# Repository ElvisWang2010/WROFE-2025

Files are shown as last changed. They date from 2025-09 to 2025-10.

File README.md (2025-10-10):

<div align="center">
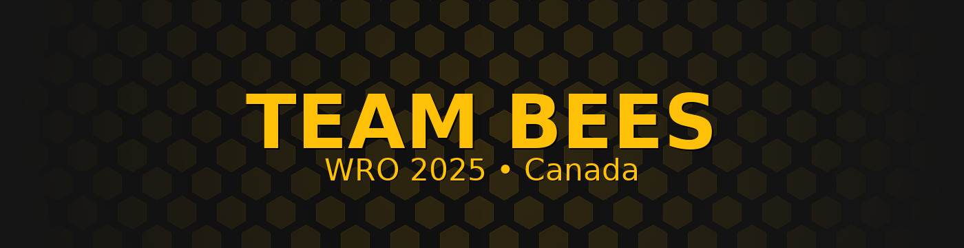
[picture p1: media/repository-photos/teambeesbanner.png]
teambeesbanner

</div>

<p align="center">
  <a href="#"><a>
  <a href="#"><a>
  <a href="#"><a>
  <a href="#"><a>
</p>

teambeesgif

<a href="https://www.youtube.com/@TeamBees2025Panama">

---

# Table of Contents

<details open>
<summary><h3>Team</h3></summary>

- [Team Members](#team-members)  
- [Team Photo](#team-photo)

</details>

---

<details>
<summary><h3>Hardware & Build</h3></summary>

- [Complete Construction Manual](#complete-construction-manual)  
- [Machinery & Components](#machinery)
- [3D Design](#3d-design-and-fabrication)
- [Assembly Gallery](#assembly-gallery)

</details>

---

<details>
<summary><h3>Mobility</h3></summary>

- [Mobility Management](#mobility-management)  
  - [Chassis](#chassis)  
  - [Drive System](#drive-system)  
  - [Motor](#motor)  
  - [Electronic Speed Controller (ESC)](#electronic-speed-controller-esc)  
  - [Steering](#steering)  
  - [Servo Motor](#servo-motor)

</details>

---

<details>
<summary><h3>Power</h3></summary>

- [Power Management](#power-management)  
  - [Battery](#battery)
  - [Power Ratings Table](#power-ratings-table)
  - [Electrical Wiring](#electrical-wiring)  
  
</details>

---

<details>
<summary><h3>Sensors & Perception</h3></summary>

- [Sense Management](#sense-management)
- [Expansion Board](#expansion-board)
- [Raspberry Pi](#raspberry-pi-5)
- [Camera](#camera)    
- [LiDAR](#lidar)

</details>

---

<details>
<summary><h3>Software</h3></summary>

- [Frameworks](#software)  
  - [Python 3.0](#python-30)  
  - [ROS 2 Humble](#ros2-humble)  
- [Libraries](#libraries)  
  - [Picamera2](#picamera2)  
  - [OpenCV](#opencv)  
  - [cv_bridge](#cv_bridge)  
  - [Time](#time)  
  - [Numpy](#numpy)  
  - [ROS Robot Controller SDK](#ros_robot_controller_sdk)

</details>

---

<details>
<summary><h3>WRO Challenges</h3></summary>

- [Open Challenge](#open-challenge)  
- [Obstacle Challenge](#obstacle-challenge)

</details>

---
</br>

## Experience

Throughout our preparation for the WRO Future Engineers competition, each of us gained new skills and experiences that went far beyond what we expected.

Months before the competition, Elvis was learning how to 3D model and 3D print custom parts for our robot. He also explored electronics in depth, learning how to wire, solder, and integrate components safely and effectively.

Harry focused on the software side, diving into ROS 2 to learn how to create nodes, build packages, and structure entire workspaces for complex multi-node communication.

Ryan improved his programming skills during the project. He learned how to properly use and navigate GitHub. He also expanded into 3D modeling.

</br>

## Our Coach
<table>
<tr>
  <td align="center" width="40%">
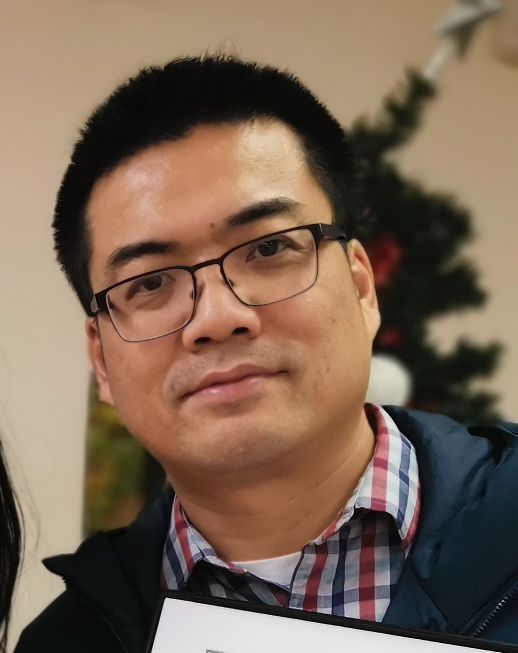
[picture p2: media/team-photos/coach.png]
    <br>
    <em>Our Coach — Mentor and Guide</em>
  </td>

  <td valign="top" width="60%">

  ### Information
  - Head coach of Robotics Competitions, including FLL (First LEGO League),  WRO (World Robotics Olympiad) Robo Sports, Future Engineers, and Robo Mission. Led teams in winning multiple national, international robotics, and programming awards.
  - Over 20 years of IT industry experience as a software engineer working internationally.
  - MSc in Electrical & Computer Engineering from the University of Alberta.
  - BSc in Mathematics from Peking University.
  - Founder of Explorer Robotics, a local robotics club in Ajax and Whitby, teaching coding, AI, robotics, etc.
  </td>
</tr>
</table>



A special thanks goes out to our amazing coach, who has been the foundation of our journey. He not only introduced us to ROS2, but was also the first person to open our eyes to the WRO Future Engineers competition and the broader world of robotics. 

## Team Members

<table width="100%" style="border:2px solid #FFC107; border-radius:12px; margin:12px 0;">
  <tr>
    <td width="28%" align="center" style="padding:12px; border-right:6px solid #111;">
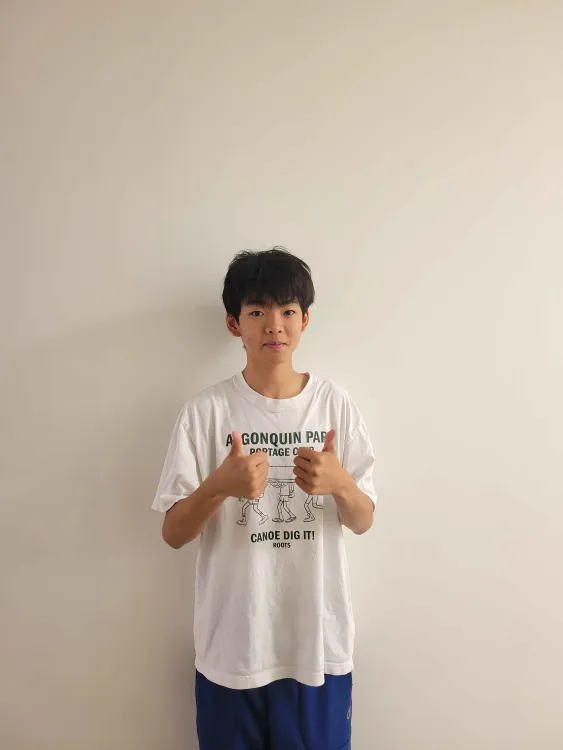
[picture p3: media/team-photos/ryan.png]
Ryan
      
    </td>
    <td width="72%" style="padding:12px 16px;">
      <h3 style="margin:0 0 6px 0;">Ryan</h3>
      <div><b>Role:</b> Documenter/Programmer</div>
      <div><b>Strengths:</b> Writing, Hardworker.</div>
      <p style="margin-top:8px;">
        <b>About Me:</b> Hi! I'm Ryan. I'm 14, love to write, play badminton, listen to music, and travel. I've been involved in robotics for nearly a decade and participated in both FLL and WRO Robo Mission. I also have a 4-year-old golden retriever 😊.
      </p>
    </td>
  </tr>
</table>

<table width="100%" style="border:2px solid #FFC107; border-radius:12px; margin:12px 0;">
  <tr>
    <td width="28%" align="center" style="padding:12px; border-right:6px solid #111;">
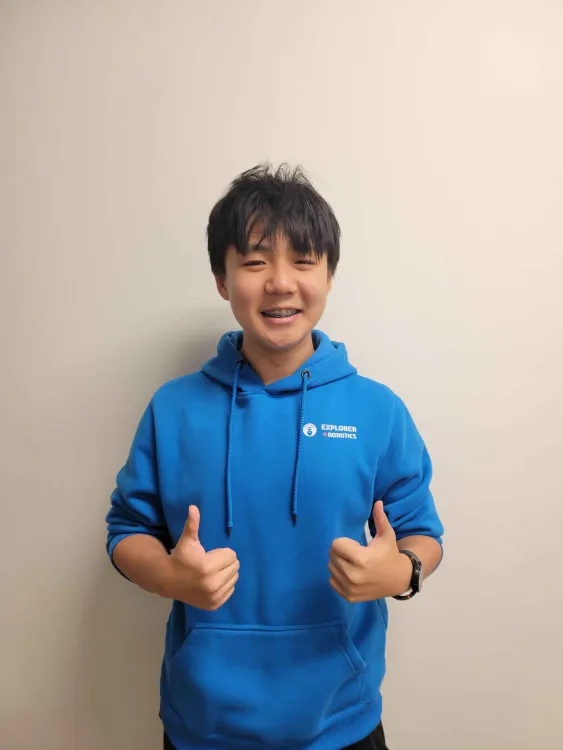
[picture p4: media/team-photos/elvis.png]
Elvis
      
    </td>
    <td width="72%" style="padding:12px 16px;">
      <h3 style="margin:0 0 6px 0;">Elvis</h3>
      <div><b>Role:</b> Builder/Programmer</div>
      <div><b>Strengths:</b> CAD, Fabrication, Team Player, Hardworker.</div>
      <p style="margin-top:8px;">
        <b>About Me:</b> Hi, my name is Elvis. I'm 14. I enjoy building and 3D modeling various objects with Fusion 360. I've been with Explorer Robotics ever since I was 8 years old, and I love to work and play Clash Royale.
      </p>
    </td>
  </tr>
</table>

<table width="100%" style="border:2px solid #FFC107; border-radius:12px; margin:12px 0;">
  <tr>
    <td width="28%" align="center" style="padding:12px; border-right:6px solid #111;">
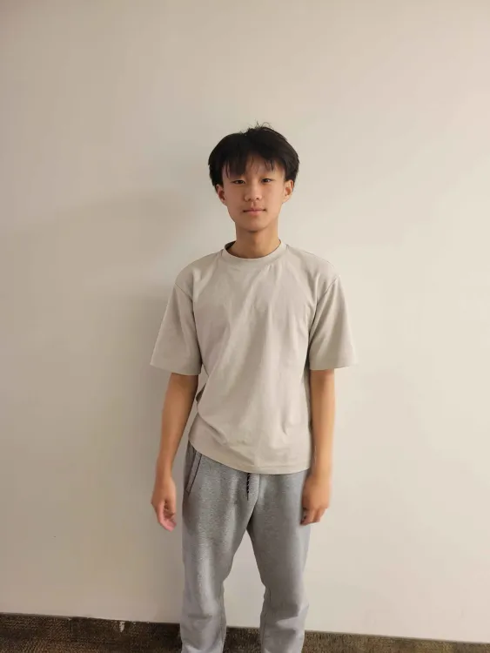
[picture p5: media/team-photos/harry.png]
Harry
      
    </td>
    <td width="72%" style="padding:12px 16px;">
      <h3 style="margin:0 0 6px 0;">Harry</h3>
      <div><b>Role:</b> Programmer/Documenter</div>
      <div><b>Strengths:</b> Python, Problem Solver, Patience, Hardworker.</div>
      <p style="margin-top:8px;">
        <b>About Me:</b> Hey! I'm Harry. I've been coding for over half a decade and enjoy swimming, having competed in various swimming competitions. I also like to play badminton.
      </p>
    </td>
  </tr>
</table>

</br>

## Introduction
Team Bees is a 1st year group of high-school students from Ontario, Canada, passionate about robotics and self-driving technologies. Our car was designed and programmed to complete both the Open and Obstacle Challenges of WRO 2025 Future Engineers. After only placing 5th in Ottawa Nationals, we advanced to Panama Internationals, representing our country.

Our objective is to design a low-cost, fully autonomous miniature car using accessible components and open-source software, integrating vision, IMU, and LiDAR for perception and ROS 2 Humble for system control.

# Team Photo

<table width="100%" style="border:2px solid #FFC107; border-radius:12px; margin:8px 0;">
  <tr>
    <td align="center" style="padding:14px;">
      <div style="border:2px dashed #FFC107; border-radius:10px; padding:24px; height:320px; display:flex; align-items:center; justify-content:center;">
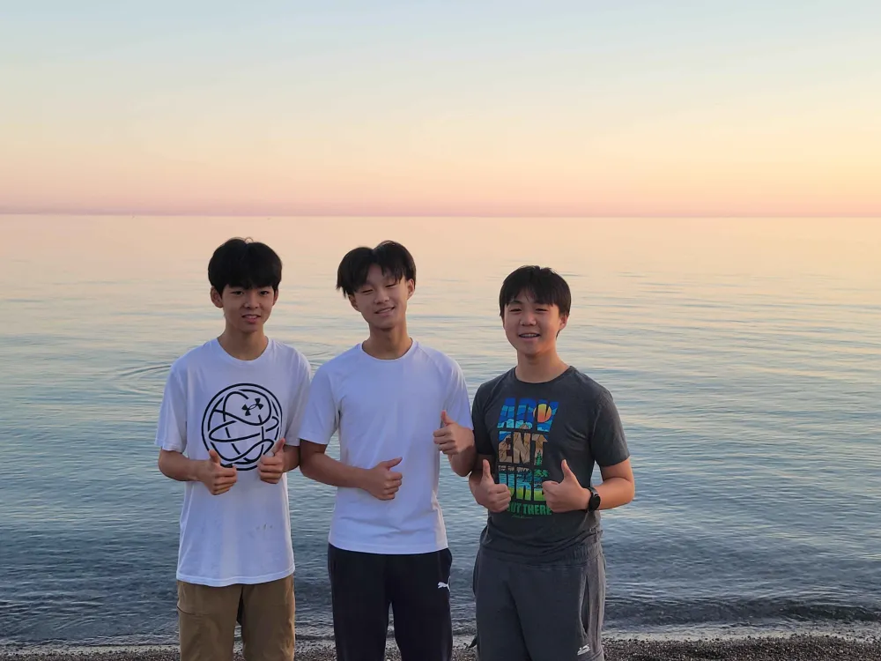
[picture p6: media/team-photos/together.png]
        <b></b>
      </div>
      <div style="margin-top:8px; color:#444;"><em>Team Bees — WRO 2025 Future Engineers (Nationals → Panama)</em></div>
    </td>
  </tr>
</table>

</div>

</br>

---

</br>

## Complete Construction Manual

The WRO Future Engineers is a competition for self-driven vehicles. Students in the 15- to 19-year-old age group need to design a model of a car, equip it with electromechanical components, and program it so that it can drive autonomously on the track, avoiding obstacles.

More details about the competition can be found on [the official site of WRO Association](https://wro-association.org/competition/2025-season/#rules).

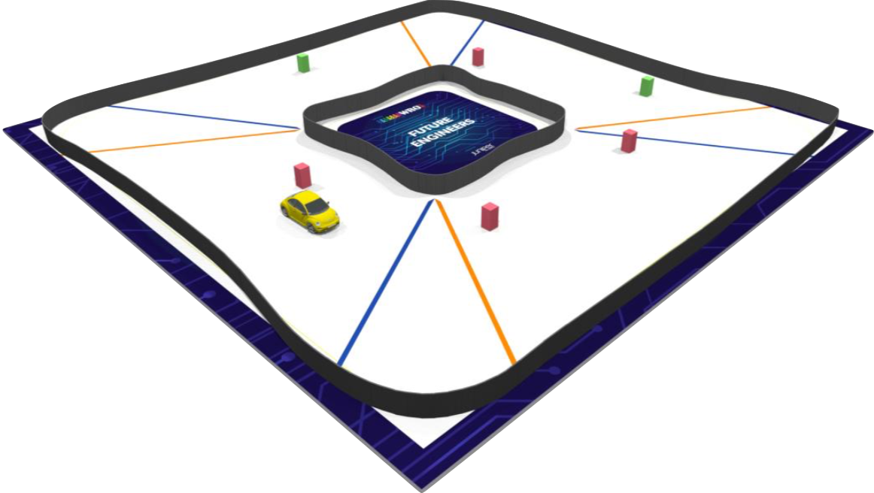
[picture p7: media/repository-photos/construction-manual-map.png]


The materials are intended to be built with the [Mkdocs](https://www.mkdocs.org/) site generator.

The example of the site is accessible at https://world-robot-olympiad-association.github.io/future-engineers-gs/.

</br>

---

</br>

## Machinery 
### Components
| Name | Product | Price (CAD)|
| --- | --- | --- |
| RC Car Battery | [`Gens Ace 1300mAh Battery`](https://genstattu.com/gens-ace-1300mah-2s-7-4v-45c-g-tech-lipo-battery-pack-with-deans-plug/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) | $20.6 | 
| Drive Motor | [`Furitek Micro Komodo 1212 3450KV Brushless Motor`](https://furitek.com/products/furitek-micro-komodo-1212-3456kv-brushless-motor-with-15t-steel-pinion-for-fury-wagon-fx118) | $35 |
| Servo Motor | [`HS-5055MG 11.9g Metal Gear Digital Micro Servo`](https://hitecrcd.com/hs-5055mg-economy-metal-gear-feather-servo/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) | $25 |
| ESC | [`Furitek Lizard Pro 30A/50A ESC`](https://furitek.com/products/combo-of-furitek-lizard-pro-30a-50a-brushed-brushless-esc-for-axial-scx24-with-bluetooth) | $80 |
| Camera | [`5MP 1080P HD Camera with OV5647 Sensor`](https://www.amazon.ca/dp/B0D324RKRZ?ref=ppx_yo2ov_dt_b_fed_asin_title) | $35 |
| Raspberry Pi 5 8GB | [`Raspberry Pi 5`](https://www.amazon.ca/RasTech-Raspberry-Pi-refroidisseur-inclus/dp/B0DQX6JPVM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) | $170 |
| Expansion Board | [`RRC Lite Controller`](https://www.hiwonder.com/products/rrc-lite?srsltid=AfmBOoqZuQkdiCruulYju-KXoSowMik5Ov_Vs3-_8TA4Bm_luvoK6Oxn) | $40 |
| Switch | [`DaierTek ON Off Round Rocker Switches`](https://www.amazon.ca/DaierTek-Listed-Switches-Automotive-KCD1-5Pack/dp/B07S1MV462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) | $2.6 |
| Wheels | [`Abendor 6 Spoke Wheel Rims`](https://www.amazon.ca/Abendor-Spoke-Narrow-Aluminum-Wltoys/dp/B09ZYVGYB4?th=1) | $31.6 |

*Note: The switch is $13 for 5. 13/5 = 2.6.*

**Total:** $439.8 *No Tax*

**With Tax:** $496.97

---

### Tools and Equipment
| Name | Product | Price (CAD)|
| --- | --- | --- |
| 3D Printer | [`Bambu Lab X1 Carbon 3D Printer`](https://genstattu.com/gens-ace-1300mah-2s-7-4v-45c-g-tech-lipo-battery-pack-with-deans-plug/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) | $1289 | 
| Soldering Kit| [`TOAUTO DS90 Soldering Station`](https://www.amazon.ca/FASTTOBUY-Soldering-Station-194%C2%B0F-896%C2%B0F-Temperature/dp/B082HP4513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) | $90 |
| Screws, Screwdriver, Pliers, etc. | n/a | $~35 |  
| Fillament 1kg | [`EconoFil™ Standard PLA Filament`](https://www.inksmith.ca/collections/filament/products/econofil-standard-pla-filament-black-1-75mm-1-kg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) | $26 |  

**Total:** $~1440 *No Tax*

**With Tax:** $~1627.2

---

### Summary of Cost
| Category | Price (CAD) No Tax| Price (CAD) Tax Included|
| --- | --- |----|
| Components | $439.8| $496.97 |
| Tools and Equipment | $1440| $1627.2 |
| Shipping | $~100 (*not taxed*)| $~100 (*not taxed*) |

**Grand Total** : $1979.8 CAD *No Tax* 

**With Tax** : $2224.17 CAD

</br>

---

## 3D Design and Fabrication

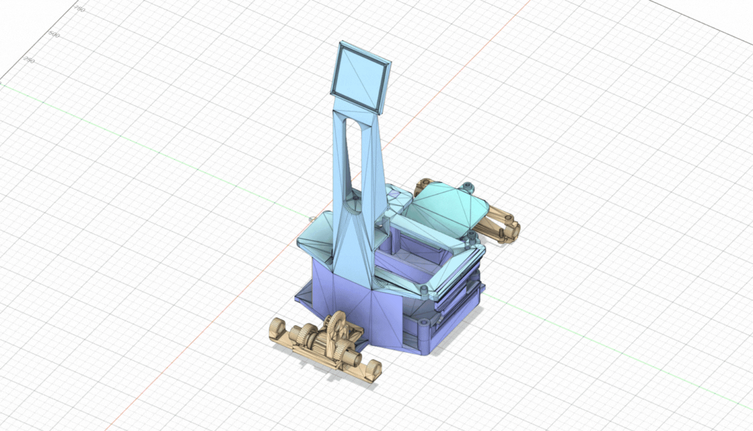
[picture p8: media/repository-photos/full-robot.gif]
|  |
|:--:|
| *Fully 3D printed design, every component custom designed* |

### Overview  
- 3D printing played a key role in our project, allowing us to design, prototype, and refine custom mechanical parts with precision and speed.  
- All major structural components, including the LiDAR mount, steering system, and motor mechanism, were modeled in Fusion and fabricated using a PS1 Bambu Lab printer with PLA filament.  
- The ability to produce rapid design iterations helped us fine-tune geometry, fit, and strength throughout testing.

---

### Printing Parameters  

| Setting | Value |
|---|---|
| Printer | [`Bambu Lab X1 Carbon`](https://ca.store.bambulab.com/products/x1-carbon?id=546459056505716744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) |
| Material | PLA (Bambu Lab Basic) |
| Nozzle Temperature | 230 °C |
| Bed Temperature | 65 °C (Textured PEI Plate) |
| Filament Diameter | 1.75 mm |
| Flow Ratio | 0.96 |
| Max Volumetric Speed | 12 mm³/s |
| Layer Height | 0.2 mm |
| Nozzle Diameter | 0.4 mm |
| Infill Density | 15 % |

---

### Why PLA?  

| Material | Strength | Heat Resistance | Printability | Availability | Notes |
|:--:|:--:|:--:|:--:|:--:|:--|
| PLA | Medium | Low | Very Easy | Widely Available | Ideal for prototypes and low-stress components. Excellent surface finish and easy to reprint. |
| PETG | High | Medium | Moderate | Common | Stronger and more flexible, but harder to print cleanly. Useful for parts under stress. |
| ABS | High | High | Difficult | Common | Better heat resistance, but warps easily and requires a heated enclosure. |
| Nylon / CF-Nylon | Very High | High | Difficult | Limited | Excellent strength and flexibility, but expensive and requires high-end printers. |

</br>

PLA was chosen for its ease of use, low cost, and availability, allowing quick iteration without sacrificing accuracy.  
It provided reliable performance for our robot, where temperature resistance and high flexibility were not critical factors.  

---

</br>

## Assembly Gallery

<table>
  <tr>
    <td align="center" style="border:1px solid #ddd; padding:15px;">
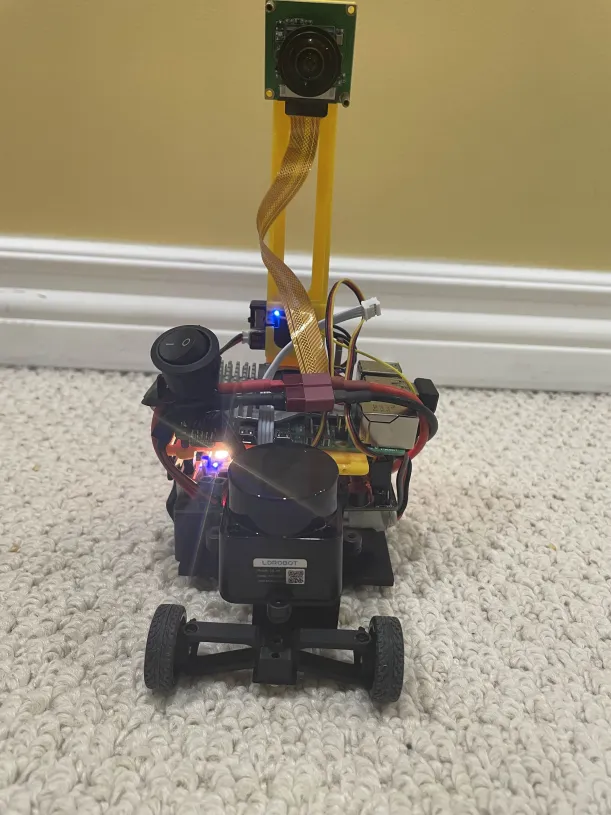
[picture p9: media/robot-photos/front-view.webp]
    <br/>
      <em><strong>Front View</strong><br>Shows the overall profile and front-facing components.</em>
    </td>
    <td align="center" style="border:1px solid #ddd; padding:15px;">
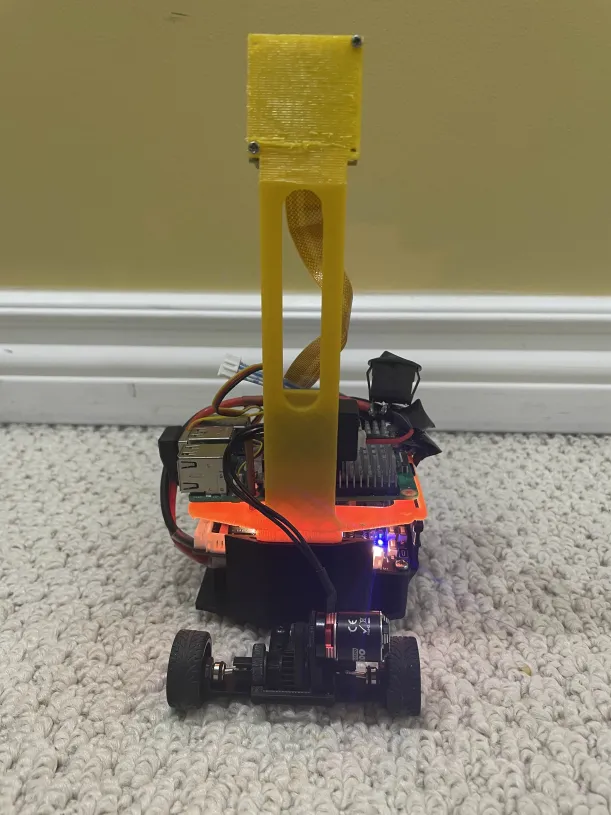
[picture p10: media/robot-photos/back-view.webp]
      <br/>
      <em><strong>Rear View</strong><br>Shows the drive wheels and rear motor assembly.</em>
    </td>
    <td align="center" style="border:1px solid #ddd; padding:15px;">
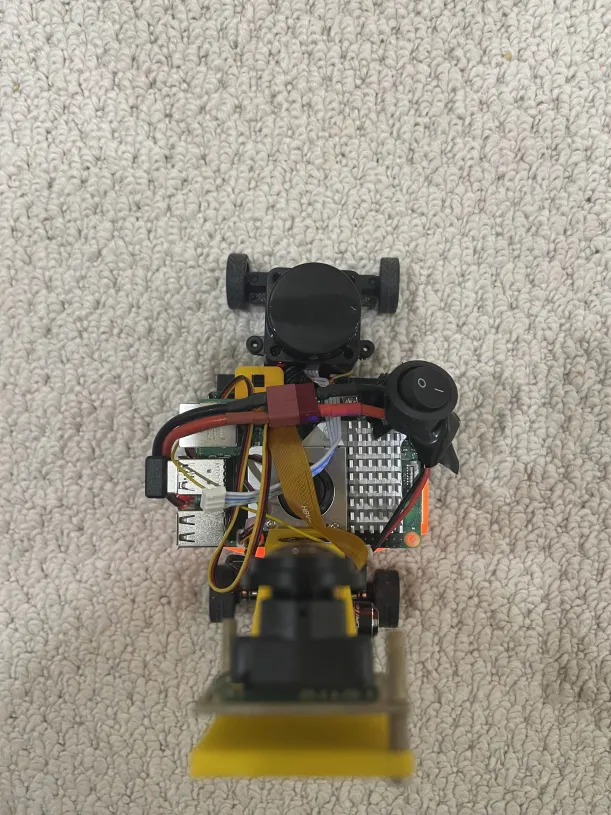
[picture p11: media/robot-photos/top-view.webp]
     <br/>
      <em><strong>Top View</strong><br>Shows the layout of all major components on the upper chassis.</em>
    </td>
  </tr>
  <tr>
    <td align="center" style="border:1px solid #ddd; padding:15px;">
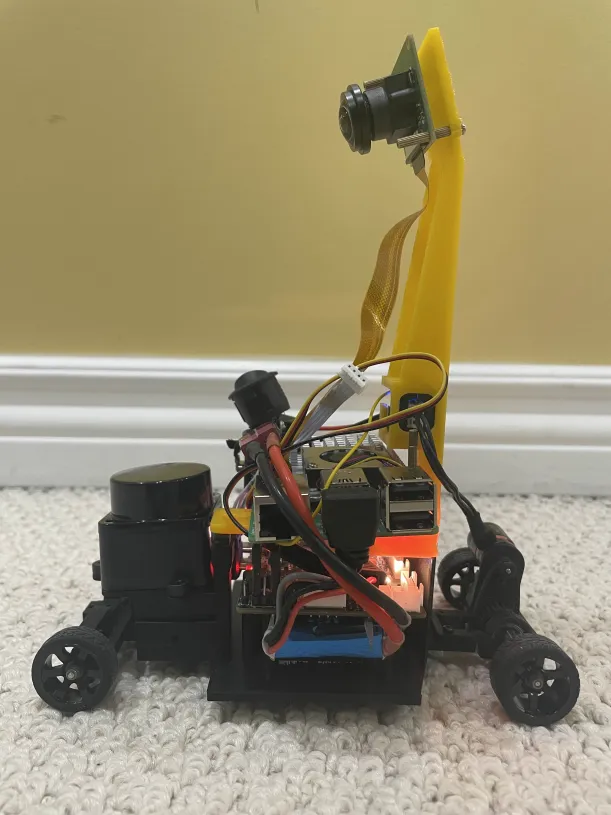
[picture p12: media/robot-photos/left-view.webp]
     <br/>
      <em><strong>Left Side View</strong><br>Shows the side profile and left-side components.</em>
    </td>
    <td align="center" style="border:1px solid #ddd; padding:15px;">
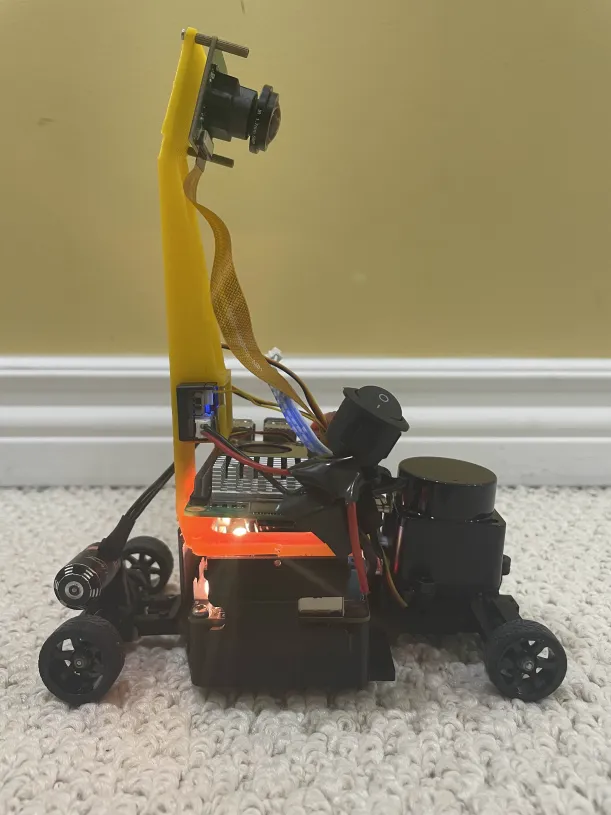
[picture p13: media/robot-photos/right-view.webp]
      <br/>
      <em><strong>Right Side View</strong><br>Shows the side profile and right-side components.</em>
    </td>
    <td align="center" style="border:1px solid #ddd; padding:15px;">
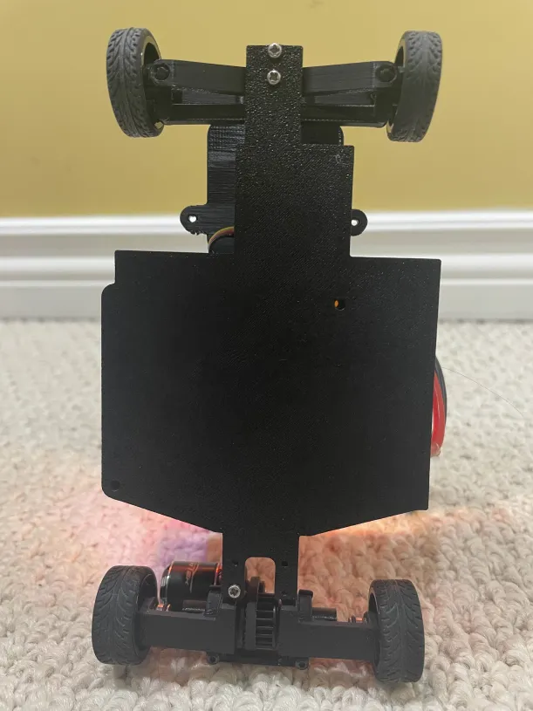
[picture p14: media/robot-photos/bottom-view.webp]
      <br/>
      <em><strong>Bottom View</strong><br>Shows the underside, wheel mounting, and lower chassis.</em>
    </td>
  </tr>
</table>

</br>

---
</br>

# Mobility Management
This section covers and houses all components that help or allow our robot to move and steer. It includes the steering system for directional control, the electronic speed controller (ESC) to manage motor power, the main motor for movement, a servo motor for precise adjustments like steering, and the chassis, which is the base to hold and support all these parts securely.

</br>

## Chassis 

We have had many chassis prototypes. For our first build, we selected the **ACXWA CD chassis**, a non-prebuilt frame originally crafted with a modular design to provide adjustable lengths between 1/28 and 1/24 scale. 
However, later on, we opted to redesign the entire chassis, 3D printing and customizing our entire robot in the process, excluding a few minor metal modules (pins, screws, etc.).

</br>

<table>
  <tr>
    <td width="48%" valign="top">
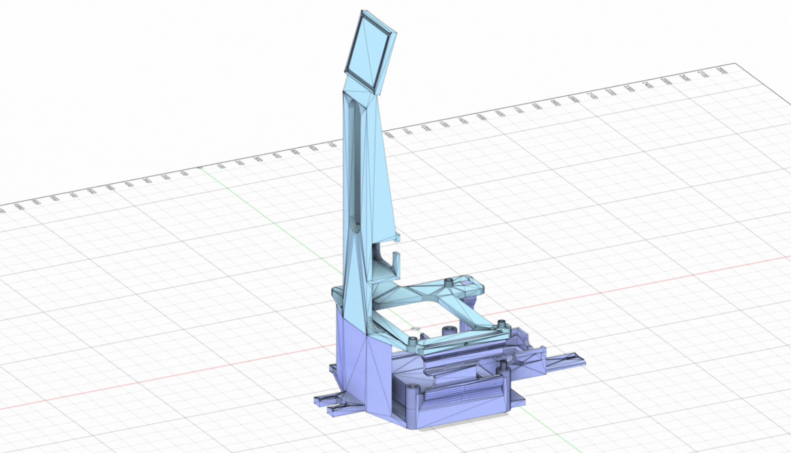
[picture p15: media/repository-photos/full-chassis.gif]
Chassis
      
      <p align="center"><em>Redesigned structural chassis assembly</em></p>
    </td>
    <td width="52%" valign="top">

### Notable Features 

- Modular design allows quick attachment of sensors, electronics, and mounts.  
- Integrated mounting rails support camera and LiDAR at optimized heights for field visibility.    
- Designed to keep the center of gravity low, improving balance and traction during movement.  

    </td>
  </tr>
</table>

---

### Chassis Limitations

Although the redesigned chassis offers significant improvements in modularity and sensor integration, it is not without challenges. The tall vertical structure increases air drag and introduces slight flex during high-speed operation, particularly when carrying additional sensors at the top. The frame’s precision mounting points demand tight tolerances, making small print variations more noticeable during assembly. Cable management also becomes more complex due to limited internal routing space, requiring external clips or channels to maintain a clean layout. 

---
### Utilization
Our custom 3D-printed chassis was carefully designed to house all the key electronic components required for our autonomous car. The lower compartment securely holds the battery and a part of the servo motor, ensuring a low center of gravity for better stability and weight distribution. Just above that, a dedicated mounting section was created for the RRC (ROS Robot Controller) expansion board. On the upper frame, we integrated a platform for the Raspberry Pi 5, which serves as the main processing unit for camera and sensor data. The long arm at the vertex of the chassis secures our camera. Right beneath it, there is a custom slot specifically designed to secure our ESC.

</br>

---

</br>

### Wheels
<div align="center">

<table>
  <tr>
    <td style="border: 200px solid black; padding: 5px;">
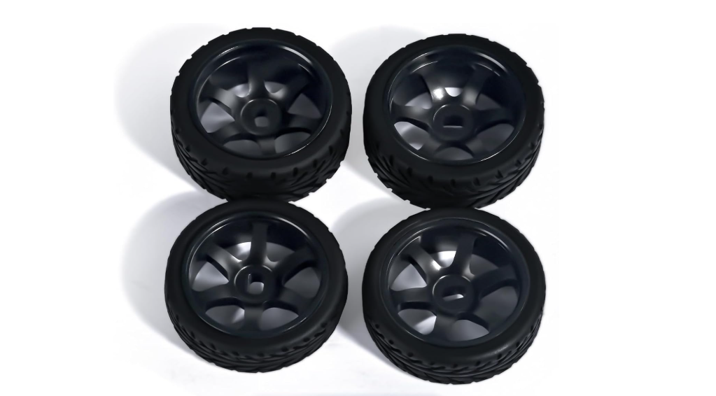
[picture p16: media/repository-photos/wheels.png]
      
    </td>
  </tr>
</table>

</div>

<p><strong>Where to Buy:</strong> <a href="https://www.amazon.ca/Abendor-Spoke-Narrow-Aluminum-Wltoys/dp/B09ZYVGYB4?th=1" target="_blank">Click Here</a></p>

</br>

Our previous wheels came with the ACXWA chassis; however, the wheels were designed to drift, and we needed to switch them out for grippier wheels. This switch had an immediate effect on the car's performance. With better traction, the vehicle could accelerate harder without losing control. It could also maintain a steady speed through turns. This made handling more predictable, which was especially important for precise tasks like navigating pillars and parking.

The new wheels also improved efficiency. With less energy wasted on wheel slip, the motor’s output went more directly into forward motion. This not only made the car feel faster but also reduced strain on the drivetrain during long runs. As a result, we had a setup that was both quicker and more reliable in competition.

</br>

## Drive System

Our car uses a rear wheel drive (RWD), meaning that the motor's power is transmitted to the back wheels rather than the front. This configuration provides many benefits to the car.

</br>

### Benefits
- Better weight distribution. This is because the front wheels handle steering, and the rear wheels help with propulsion, which helps the car remain more balanced during acceleration and turning.
- RWD also provides a stronger grip on surfaces. Since the rear of the robot is heavier, the back wheels get pressed into the ground, providing for more traction and therefore enhancing the grip.
- Since the front wheels are only used for steering, the car can turn more precisely, as there is no motor interference.

</br>

## Motor

---

<table>
<tr>
  <td width="35%" valign="top">

  ### Physical Qualities
  | Field          | Value                              |
  |----------------|------------------------------------|
  | **Product Title** | Furitek Micro Komodo 1212 3450KV |
  | **Size**          | 15.5 × 20.6 mm                   |
  | **Weight**        | 17.5 g                           |
  | **Physical State**| Brushless Outrunner (12-slot)    |

  </td>

  <td width="65%" align="center">
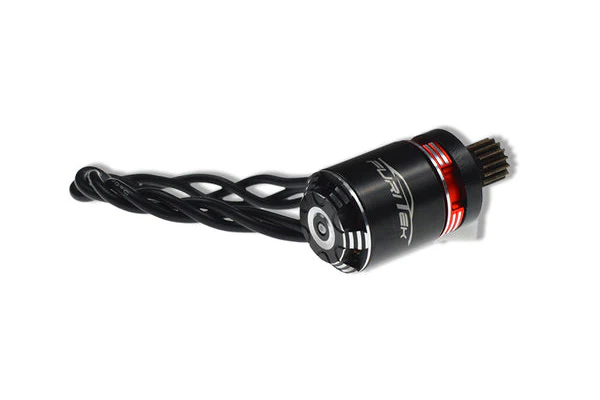
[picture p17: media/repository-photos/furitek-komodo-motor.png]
    <br>
    <em>Furitek Komodo 1212 motor</em>
  </td>
</tr>
</table>

---

<table>
<tr>
<td width="65%" valign="top">

### Reasoning of Purchase
Following a review of suitable brushless options, we selected the Furitek Micro Komodo 1212 3450 KV brushless motor. This motor is compact and lightweight, making it perfect for a small self-driving platform where space and weight impact agility and energy use. Its 12-slot, multipole design distributes torque more evenly during rotation. This results in less cogging, smoother throttle response, and better control at low speeds.

---

### Potential Improvements
- Replace plastic gears with metal gears to withstand sustained, high-speed usage.
- Experiment with 10 : 58 – 14 : 58 combinations to tune the balance between torque and top speed.
- Upgrade or lubricate bearings to reduce friction and improve consistency over multiple heats.
  
</br>

</td>

<td width="35%" valign="top">

### Performance Specifications
- KV: **3450 rpm/V**  
- No-load @10V: **0.7 A**  
- Power: **120 W**  
- Battery: **2–3S LiPo**  
- Resistance: **0.16 Ω**  
- Max Current: **10 A**  
- Slot/Pole: **12**  
- Shaft: **1.5 × 6 mm**  

</td>
</tr>
</table>

---

<p><strong>Where to Buy:</strong> <a href="https://furitek.com/products/furitek-micro-komodo-1212-3456kv-brushless-motor-with-15t-steel-pinion-for-fury-wagon-fx118" target="_blank">Click Here</a></p>

</br>

To secure the motor to the chassis, we 3D printed a motor mechanism with a slot designed to fit the motor's axle.

</br>

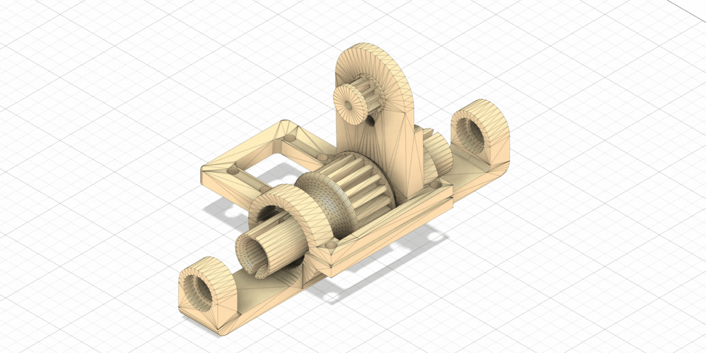
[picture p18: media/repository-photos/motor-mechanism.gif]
|  |
|:--:|
| **Motor Mechanism** |

</br>

This 3D-printed motor gear mount assembly connects the brushless motor to the drivetrain using a fixed spur gear reduction system. The motor’s pinion drives a larger spur gear on the output shaft, which reduces speed and increases torque. The mount has a sturdy motor plate, gear supports that fit bearings, and a reinforced base that keeps both shafts aligned. This setup ensures smooth power transfer and consistent gear meshing. The design reduces energy loss and mechanical vibration from misalignment while remaining lightweight and compact. 

### Potential Improvements
- Implement a stronger motor holder to cut down on vibration and improve stability when it's under load.
- Explore different motor designs to improve performance and reduce weight.

## Electronic Speed Controller (ESC)  
The ESC is a key component that regulates how the motor receives power. It:  
- Controls the motor's speed  
- Manages direction  
- Ensures safe delivery of voltage and current to the motor

This ESC was chosen for its high current capacity, lightweight design, and reliable built-in BEC, making it well-suited for our motor and servo needs.

</br>

<table border="1" width="100%" style="font-size:20px; text-align:left;">
  <tr> 
    <td width="50%" align="center" style="vertical-align:top;"> 
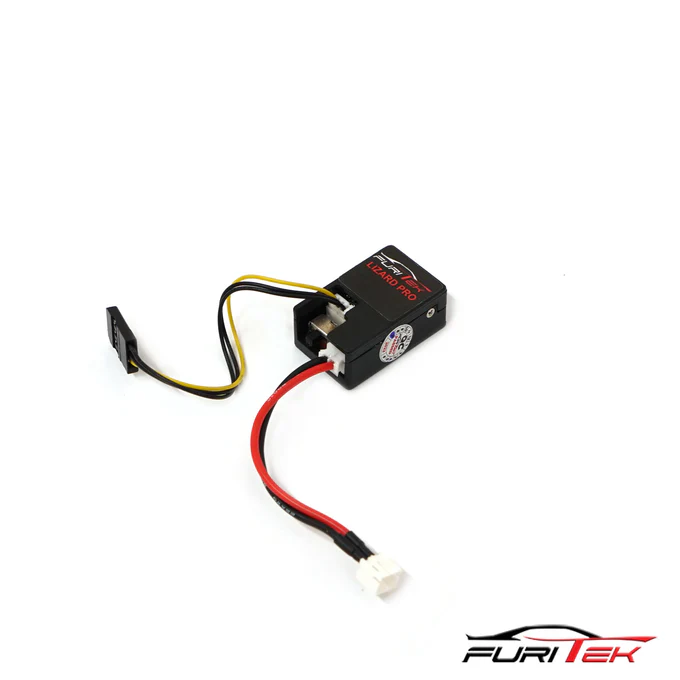
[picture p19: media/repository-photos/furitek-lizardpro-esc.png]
       
    </td> 
    <td width="50%" valign="top" style="vertical-align:top; font-size:20px;"> 
         <h2 style="font-size:28px;">Furitek Lizard Pro 30A/50A ESC</h2> 
      <ul>
        <li><strong>Battery Support:</strong> 2S–3S LiPo</li> 
        <li><strong>BEC:</strong> 5V or 6.5V, 2.5A</li> 
        <li><strong>Constant Current:</strong> 30A</li> 
        <li><strong>Burst Current:</strong> 50A</li> 
        <li><strong>Built-in Power Switch</strong></li> 
        <li><strong>Dimensions:</strong> 28 × 15.5 mm</li> 
        <li><strong>Weight:</strong> 3.7 g</li> 
      </ul> 
    </td> 
  </tr> 
</table>

<p><strong>Where to Buy:</strong> <a href="https://furitek.com/products/combo-of-furitek-lizard-pro-30a-50a-brushed-brushless-esc-for-axial-scx24-with-bluetooth" target="_blank">Click Here</a></p>

</br>

---

## Servo Motor

This servo motor was chosen for its compact size, strong torque, and durable metal gears, making it great for precise steering control.

</br>

<table border="1" width="100%" style="font-size:20px;">
  <tr>
    <td width="50%" align="center" style="vertical-align:top;">
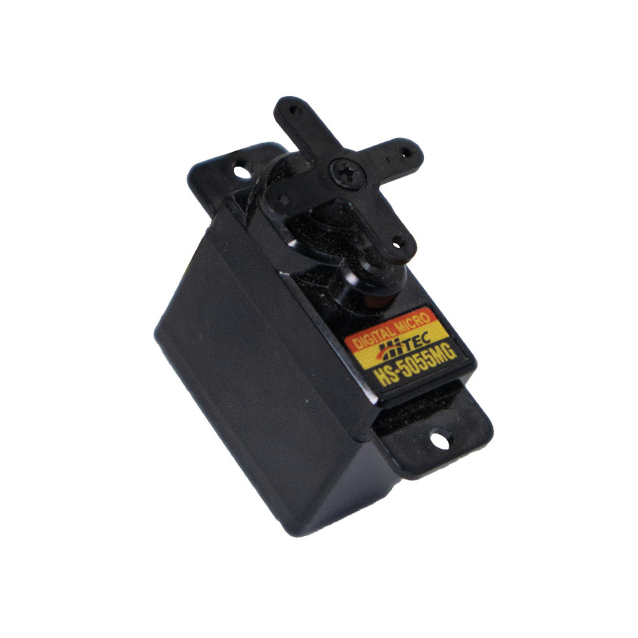
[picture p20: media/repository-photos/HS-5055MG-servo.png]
      
    </td>
    <td width="50%" valign="top" style="vertical-align:top; font-size:20px;">
      <h2 style="font-size:26px;">HS-5055MG 11.9g Metal Gear Digital Micro Servo</h2>
      <ul>
        <li><strong>Operating Voltage:</strong> 4.8V – 6.0V DC</li>
        <li><strong>Max Torque:</strong> 22 oz/in (1.6 kg/cm)</li>
        <li><strong>Speed:</strong> 0.17s/60° @ 6.0V</li>
        <li><strong>Stall Current:</strong> 700 mA</li>
        <li><strong>Gear Material:</strong> Metal</li>
        <li><strong>Weight:</strong> 9.5 g</li>
        <li><strong>Circuit Type:</strong> G1 Programmable Digital</li>
      </ul>
    </td>
  </tr>
</table>

<p><strong>Where to Buy:</strong> <a href="https://hitecrcd.com/hs-5055mg-economy-metal-gear-feather-servo/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" target="_blank">Click Here</a></p>

</br>

### Potential Improvements
- Improve response time. This servo motor is not as quick as higher-end micro servos, which reduces steering precision during sharp turns.
- Upgrade to a higher-torque digital micro servo for more reliable steering.

</br>

## Steering
Our prototype used a commercial chassis. We quickly found that the steering system was inefficient and turned unevenly. To fix this, we built a completely new steering system from scratch, 3D-printing all the components for the precise and balanced control we needed. We developed two different steering designs. The first design includes a mounting frame that attaches the system to the chassis, a servo linkage arm that connects directly to the servo motor, and steering knuckles. However, the second design showed more potential. After testing, it performed better than the first design. This design features an antisway arm, steering knuckles, and a control arm, offering a more consistent turn, easier assembly, and greater durability.

</br>

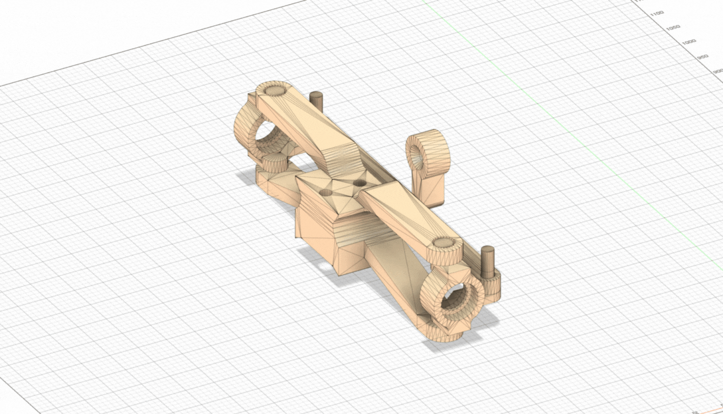
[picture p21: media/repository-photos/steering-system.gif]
|  |
|:--:|
| **Steering System** |

</br>

### Key Improvements Over Stock Design
1. **Symmetry in Motion** – Both left and right wheels now turn at equal angles, reducing understeer/oversteer imbalance.  
2. **Reduced Backlash** – By using strong linkages and tightly toleranced 3D-printed parts, uncontrolled movement is minimized.  
3. **Strength & Durability** – The mounting frame distributes servo torque evenly, reducing wear and preventing chassis flex.  
4. **Precision Control** – The redesigned geometry allows finer servo adjustments to translate directly into steering corrections.
   
</br>

- Add more fillets on corners, reducing stress concentration and preventing cracks.
- Implement brass threaded inserts for screw holes rather than relying on bare plastic.

</br>

### How the Car Moves
When the battery provides power, the ESC manages the electricity sent to the motor. The motor turns this controlled flow of electricity into rotational motion, which makes the car's wheels spin. By changing the voltage and current through the ESC, we can control the car's speed and direction, enabling it to move forward, backward, accelerate, slow down, or reverse.

At the same time, the servo motor handles steering. It changes the angle of the front wheels through the steering system, allowing the car to turn left or right accurately.

---

</br>

# Power Management

The robot’s power system is carefully designed to balance performance and efficiency, ensuring stable operation throughout the challenge.

</br>

## Battery

---

<table>
<tr>
  <td valign="top" width="35%">

  ### Physical Qualities
  | Field | Value |
  |--------|--------|
  | Product Title | Gens Ace 1300mAh 2S 7.4V 25C LiPo |
  | Size | 70.9 × 35.2 × 14.5 mm |
  | Weight | 90 g |
  | Type | 2S1P LiPo Battery |
  | Connector | T-Style (Battery), G-Tech Smart (Balance) |

  </td>

  <td align="center" width="65%">
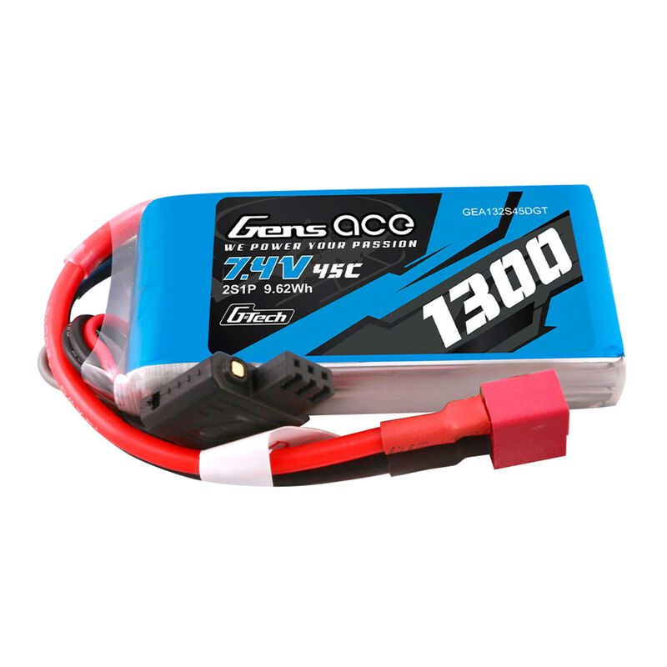
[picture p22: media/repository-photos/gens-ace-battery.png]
    <br>
    <em>Gens Ace 1300mAh 2S LiPo Battery</em>
  </td>
</tr>
</table>

---

<table>
<tr>
<td valign="top" width="65%">

### Reasoning of Purchase
We selected the Gens Ace 1300mAh 2S LiPo for its excellent balance between weight, capacity, and current output.  
Its 45C continuous (90C burst) discharge rate provides strong acceleration without noticeable voltage drop.  
The compact design keeps our self-driving car lightweight and well-balanced, ideal for quick maneuvers on WRO courses.  
Its 7.4V rating offers stable power delivery without the extra wear that 3S (11.1V) packs can cause on smaller ESCs and motors.

---

### Potential Improvements
- Increase capacity to 1500–1800mAh for longer runtime between charges.  
- Support faster charging by using a pack with higher C-rate.  
- Add built-in protection for overcharge or over-discharge safety.  

</br>

</td>

<td valign="top" width="35%">

### Performance Specifications
- Voltage: 7.4V (2S)  
- Capacity: 1300mAh  
- Discharge Rate: 45C Continuous / 90C Peak  
- Charge Rate: 5C (6.5A Max)  
- Cell Configuration: 2S1P  
- Watt Hours: 9.62Wh  

</td>
</tr>
</table>

---

<p><strong>Where to Buy:</strong> <a href="https://www.aliexpress.com/item/1005007495175639.html?spm=a2g0o.order_list.order_list_main.11.48a11802NKINMb" target="_blank">Click Here</a></p>

The battery is located at the lowest point of the chassis and is securely attached with Velcro. 
</br>

### Power Ratings Table
| Component | Voltage | Normal Current Draw | Max Current Draw | Normal Power | Max Power |
|-|-|-|-|-|-|
| 5MP 1080P HD Camera | 5 V | 0.16 A | 0.20 A | 0.80 W  | 1.00 W  |
| RRC Lite Controller | 5 V | 0.07 A | 0.50 A | 0.35 W  | 2.50 W  |
| Furitek Lizard Pro ESC | 7.4 V | 0.007 A  | 0.10 A | 0.05 W  | 0.74 W  |
| Furitek Micro Komodo Motor  | 7.4 V | 0.95 A | 10.0 A | 7.00 W  | 74.0 W  |
| HS-5055MG Servo Motor | 5 V | 0.10 A | 0.70 A | 0.50 W  | 3.50 W  |
| MicroSD, LEDs, Speakers | 5 V | 0.12 A | 0.30 A | 0.60 W  | 1.50 W  |
| Raspberry Pi 5 | 5 V | 0.55 A | 2.00 A | 2.75 W  | 10.0 W  |
| Expansion Board | 5 V | 0.12 A | 0.50 A | 0.60 W  | 2.50 W  |
| Totals | — | — | — | ~12.5 W | ~95 W |

</br>

The **Gens Ace 1300 mAh 2S 7.4 V LiPo Battery** offers plenty of power for our car, as shown in the Power Ratings Table. Normally, the car uses about 13 W, which is about 1.7 A from the battery. The car typically draws around 4 W (≈0.5 A) and, in short bursts, can reach 97 W (≈13 A). The 7.4 V 1300 mAh LiPo has a 45C continuous and 90C peak rating, meaning it can safely supply up to 58.5 A continuously and 117 A in short bursts, far more than the car will ever require. This extra capacity allows the battery to provide stable voltage for the Raspberry Pi, controller, sensors, and peripherals.

</br>

### Estimated Runtime

| Scenario | What’s on | Battery current | Runtime 80% | Runtime 85% |
|---|---|---:|---:|---:|
| Idle (no camera)  | RPi 5, RRC Lite, Expansion board, misc, ESC idle | ~0.59 A | ~106 min | ~112 min |
| Idle + camera | Above + camera streaming | ~0.70 A | ~89 min | ~95 min |
| Driving (typical) | Idle + camera + drive motor (normal) + steering servo active | ~1.71 A | ~37 min | ~39 min |

#### Assumptions: 
- In practice, you usually only use ~80–85% of the rated capacity (≈1.04–1.105 Ah).  
- Power sums taken from your Normal Power column and converted at 7.4 V.  

</br>

---

</br>

## Electrical Wiring

<div align="center">

<table>
  <tr>
    <td style="border: 200px solid black; padding: 5px;">
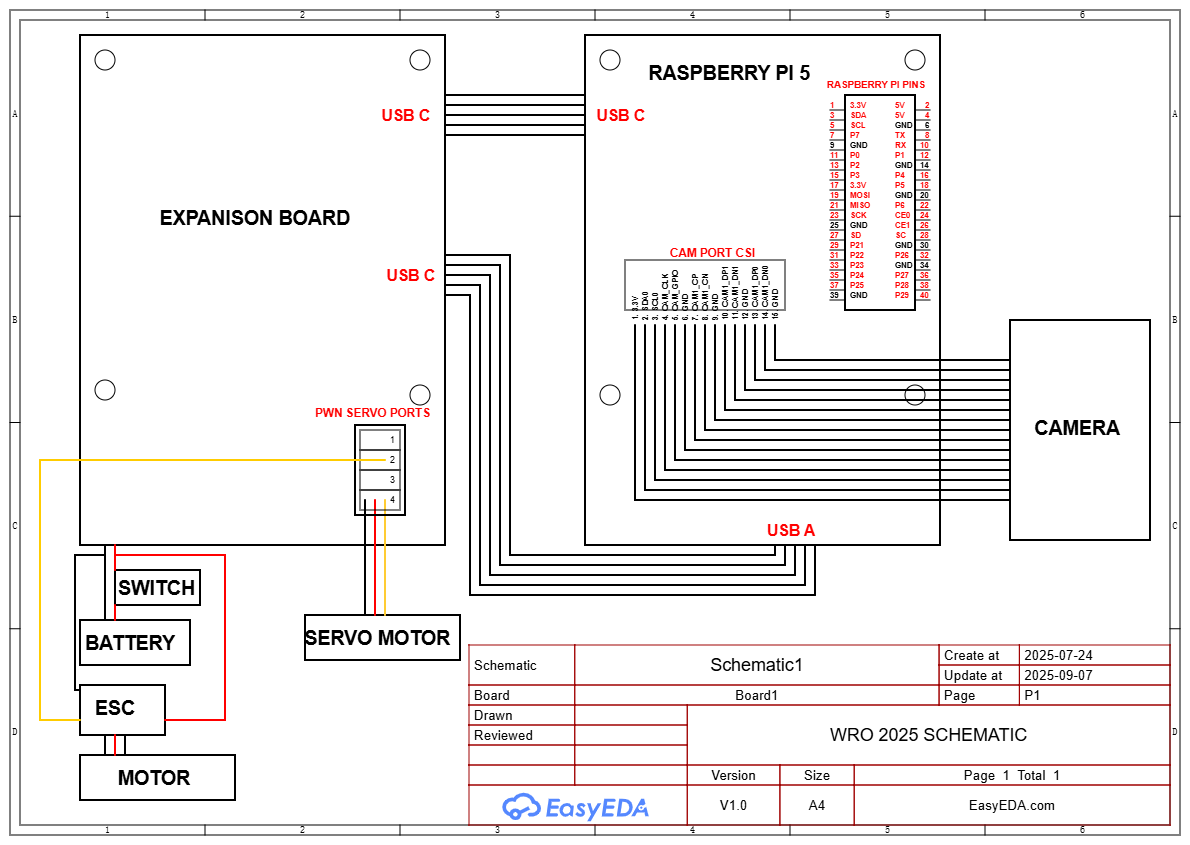
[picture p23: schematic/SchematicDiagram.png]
SCH_Schematic1_1-P1_2025-09-07
      
    </td>
  </tr>
</table>

</div>

### Components

- Raspberry Pi 5
- Expansion Board
- Camera
- Servo Motor
- ESC (Electronic Speed Controller)
- Motor
- Battery
- Switch

### Connections

#### Raspberry Pi 5
- **USB-C** ↔ Expansion Board 
- **USB-A** ↔ Expansion Board 
- **CAM PORT CSI** ↔ Camera (15-pin ribbon)

#### Expansion Board
- **PWM Servo Ports**
  
Channel 1 (unused) → Signal | +5V | GND

Channel 2 (ESC) → Signal (ESC) | +5V  | GND

Channel 3 (unused) → Signal | +5V | GND

Channel 4 (Servo) → Signal (Servo) | +5V (Servo) | GND (Servo)

#### Motor Power
Battery (+) → Switch → ESC → Motor
ESC also connects to the Expansion Board for monitoring/control

#### Wire Color Codes
*NOTE: Not all wires are color coded*

**Red:** VCC / Positive power
**Black:** GND / Ground
**Yellow:** PWM / Control signal

We used a soldering machine to securely connect wires, preventing loose connections and any erratic losses of power.

</br>

---

</br>

# Sense Management

The car relies on various sensors to understand its surroundings and interact safely with the environment. Sense management refers to how these inputs are coordinated, processed, and used for decision-making. Instead of treating each sensor independently, we designed a system that combines all data into a single model of the world. 

</br>

## Expansion Board

---

<table>
<tr>
  <td valign="top" width="40%">

  ### Physical Qualities
  | Field | Value |
  |--------|--------|
  | Product Title | Hiwonder RRC Lite Controller |
  | Size | 85 × 56 × 17 mm |
  | Weight | 32 g |
  | Power Supply | 6–14 V DC |
  | Mounting Pitch | 57.5 × 48.5 mm |

  </td>

  <td align="center" width="60%">
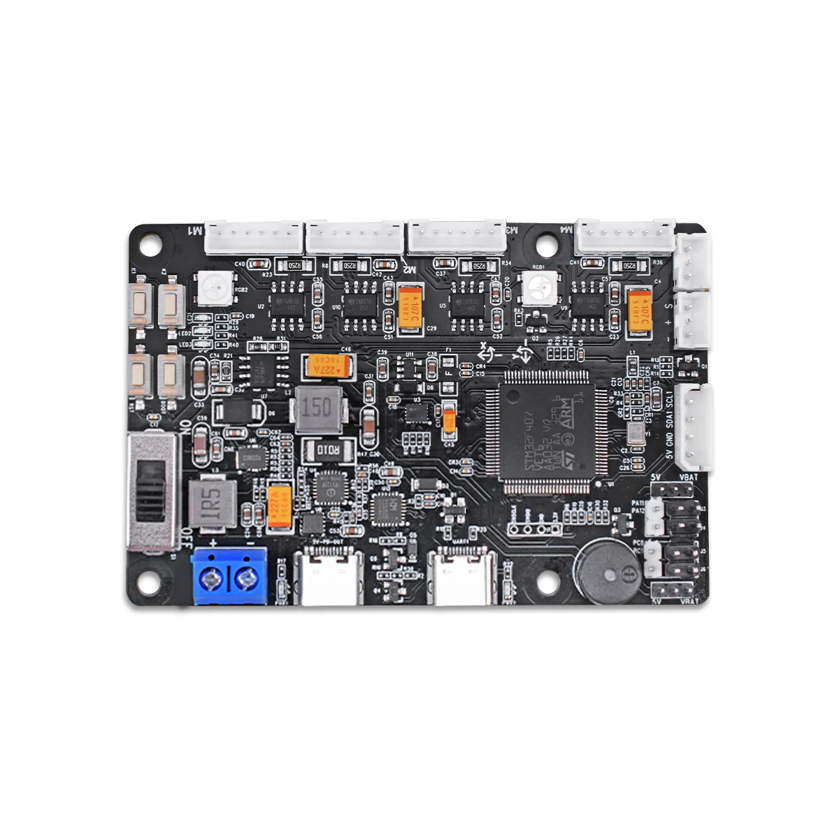
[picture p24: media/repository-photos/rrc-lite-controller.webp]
    <br>
    <em>Hiwonder RRC Lite Controller Board</em>
  </td>
</tr>
</table>

---

<table>
<tr>
<td valign="top" width="65%">

### Reasoning of Use
We selected the Hiwonder RRC Lite Controller as the central control unit for our self-driving car.  
It provides a compact yet powerful platform capable of handling motor control, IMU feedback, and servo operation all in one board.  
Its integrated IMU sensor enables precise lap counting and orientation tracking, while the built-in motor drivers reduce the need for external hardware.  

---

### Potential Improvements
 Our expansion board is quite cluttered, and the wires aren't properly managed. Wire management is crucial to a neat and properly designed robot, as it helps with airflow and modularity.
</br>

</td>

<td valign="top" width="35%">

### Performance Specifications
- MCU: STM32F407VET6 (100-pin)  
- Motor Driver: SA8870C (Overcurrent Protection)  
- IMU: 3-axis accelerometer + 3-axis gyroscope  
- Motor Encoder Ports: 4 Independent Channels  
- PWM Servo Ports: 4 (5–8.4V)  
- Serial Servo Ports: 2 (6–12V)  
- Indicators: 3 LEDs, 2 RGB LEDs, 1 Buzzer  
- External Power: 5V 5A  

</td>
</tr>
</table>

---

<p><strong>Where to Buy:</strong> <a href="https://www.hiwonder.com/cdn/shop/files/1_39aaca4a-992b-4976-b21c-6a53e3ac99a9.jpg?v=1726816513%201200w" target="_blank">Click Here</a></p>

---

| Bottom Chassis |
|:--:|
| **Bottom Chassis** |

As mentioned in the [Chassis](#chassis) section, this base chassis securely houses the battery, part of the servo motor, and the expansion board.

---

## Raspberry Pi 5 

---

<table>
<tr>
  <td valign="top" width="35%">

  ### Physical Qualities
  | Field | Value |
  |--------|--------|
  | Product Title | RasTech Raspberry Pi 5 Kit (8GB RAM) |
  | Dimensions | 15 × 9.9 × 3.9 cm |
  | Weight | 70 g |
  | Included | Pi 5 Board, Case, Active Cooler, Screwdriver |
  | Manufacturer | Vemico |
  | Wireless | 802.11ac Wi-Fi, Bluetooth |

  </td>

  <td align="center" width="65%">
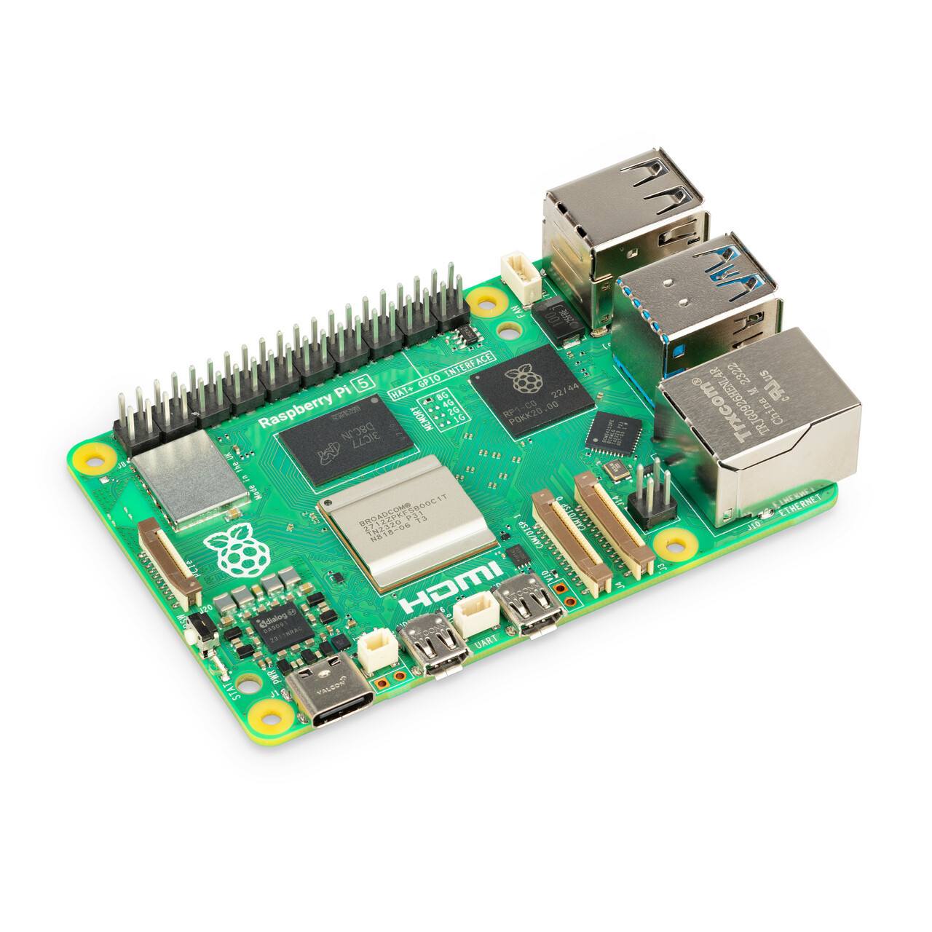
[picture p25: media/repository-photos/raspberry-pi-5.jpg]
    <br>
    <em>Raspberry Pi 5</em>
  </td>
</tr>
</table>

---

<table>
<tr>
<td valign="top" width="65%">

### Reasoning of Purchase
The main brain of our robot is a Raspberry Pi 5, which takes care of the system via computer vision, LiDAR data interpretation, and decision-making algorithms.
Just like that, it is the perfect combination of processing power and energy consumption, making it very suitable for the execution of Python scripts and OpenCV tasks.

---

### Potential Improvements
- Find more use for the GPIO pins
- Place the Raspberry Pi 5 lower on our robot to lower the center of gravity. The Raspberry Pi is a heavy component relative to others, heavily influencing weight distribution.

</br>

</td>

<td valign="top" width="35%">

### Performance Specifications
- Processor: Broadcom BCM2712, Quad-Core Cortex-A76 @ 2.4 GHz  
- RAM: 8 GB LPDDR4X-4266  
- GPU: VideoCore VII (Integrated)  
- Storage: microSD  
- Ports: 2× USB 3.0, 2× USB 2.0, 2× micro HDMI, Ethernet, GPIO  
- OS: Raspberry Pi OS (Raspbian)  

</td>
</tr>
</table>

---

<p><strong>Where to Buy:</strong> <a href="https://www.amazon.ca/RasTech-Raspberry-Pi-refroidisseur-inclus/dp/B0DQX6JPVM" target="_blank">Click Here</a></p>

</br>

---

</br>

## Camera
This camera was chosen for its wide 175° field of view, compact size, and 5MP resolution, making it ideal for real-time vision processing and object detection on our car.  
</br>

<table border="1" width="100%" style="font-size:20px; text-align:left;">
  <tr> 
    <td width="50%" align="center" style="vertical-align:top;"> 
      <img width="500 alt="image" src="media/repository-photos/5zero-camera-module.png" />
    </td> 
    <td width="50%" valign="top" style="vertical-align:top; font-size:20px;"> 
      <h2 style="font-size:28px;">5/Zero Camera Module (OV5647 Sensor)</h2> 
      <ul>
        <li><strong>Lens Pixel:</strong> 5 MP</li> 
        <li><strong>Resolution:</strong> 2592 × 1944</li> 
        <li><strong>Lens Angle:</strong> 175° Wide Angle</li> 
        <li><strong>Lens Focal Length:</strong> 3.6 mm</li> 
        <li><strong>Focus Mode:</strong> Manual</li> 
        <li><strong>CMOS Size:</strong> 1/2.5 inch</li> 
        <li><strong>Material:</strong> ABS + Optical Glass</li> 
        <li><strong>Screw Model:</strong> M2 × 6</li> 
        <li><strong>Cable:</strong> 15 cm Ribbon Cable</li> 
      </ul> 
    </td> 
  </tr> 
</table>

<p><strong>Where to Buy:</strong> <a href="https://www.amazon.ca/dp/B0D324RKRZ?ref=ppx_yo2ov_dt_b_fed_asin_title" target="_blank">Click Here</a></p>

</br>

The wide-angle camera serves as the car’s primary tool for visual detection. With its 175° lens, the camera captures almost the entire forward field of view, reducing blind spots and enabling the system to track multiple objects simultaneously. This feature proves particularly useful for tasks like pillar and wall detection, identifying obstacles ahead, and observing changes in the environment.

We process the camera feed on the Raspberry Pi using computer programs. This setup allows the car to not only notice when something is in its path but also to identify what it is, such as open passages, furniture, people, or, in this case, walls and pillars. This understanding gives the car a significant edge over systems that depend solely on distance sensors.

</br>

---

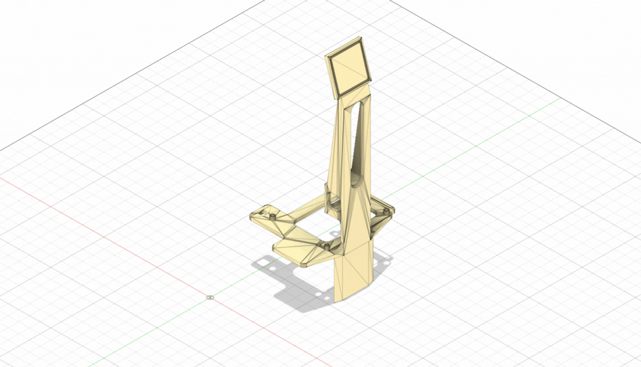
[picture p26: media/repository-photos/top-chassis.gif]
|  |
|:--:|
| **Top Chassis** |

Mentioned in the [Chassis](#chassis) section, the top chassis houses our camera, ESC, and Raspberry Pi 5.

--- 

### Potential Improvements

While the current Pi Camera provides a good amount of sensing for our obstacle challenge, several improvements could improve performance.

**Camera (5MP Pi Camera w/ OV5647)**
- Upgrade to a higher resolution or global-shutter sensor (e.g., HQ Camera IMX477) for sharper images and less motion blur.  
- Add auto exposure and white balance adjustments to handle changing lighting conditions.    
- Explore infrared capability with an IR-sensitive camera and an IR light source for consistent performance regardless of ambient lighting.  
- Apply filtering in software (e.g., erosion/dilation in OpenCV) or use a moving average/Kalman filter to stabilize pillar tracking.

</br>

### Lidar 

This LiDAR is good for its long-range accuracy, compact design, and robust scanning capability, making it ideal for mapping and obstacle detection in our car.  

<table border="1" width="100%" style="font-size:20px; text-align:left;">
  <tr> 
    <td width="50%" align="center" style="vertical-align:top;"> 
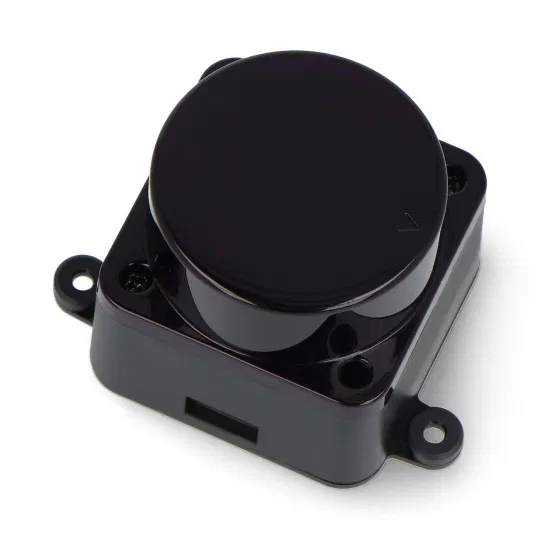
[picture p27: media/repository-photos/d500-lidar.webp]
LDROBOT D500 LiDAR
       
    </td> 
    <td width="50%" valign="top" style="vertical-align:top; font-size:20px;"> 
      <h2 style="font-size:28px;">LDROBOT D500 LiDAR</h2> 
      <ul>
        <li><strong>Ranging Distance:</strong> 0.03 – 12 m</li> 
        <li><strong>Accuracy:</strong> ±10 mm (0.3–0.5 m), ±20 mm (0.5–2 m), ±30 mm (2–12 m)</li> 
        <li><strong>Scanning Angle:</strong> 360°</li> 
        <li><strong>Scanning Frequency:</strong> 6 – 13 Hz (Typ. 10 Hz)</li> 
        <li><strong>Ranging Frequency:</strong> 5000 Hz</li> 
        <li><strong>Wavelength:</strong> 895 – 915 nm (Typ. 905 nm)</li> 
        <li><strong>Interface:</strong> UART @ 230400 baud</li> 
        <li><strong>Ambient Light Tolerance:</strong> up to 60K Lux</li> 
        <li><strong>Power Supply:</strong> 5 V</li> 
        <li><strong>Power Consumption:</strong> 1.45 W (290 mA)</li> 
        <li><strong>Operating Temperature:</strong> -10 ~ 45 °C</li> 
        <li><strong>Dimensions:</strong> 54 × 46.3 × 35 mm</li> 
        <li><strong>Weight:</strong> 45 g</li> 
      </ul> 
    </td> 
  </tr> 
</table>

</br>

The LiDAR is the car’s most reliable tool for precise distance measurement and mapping. Unlike a camera, which depends on good lighting and struggles to estimate exact distances, the LiDAR provides accurate range data in every direction, up to 12 meters away. This gives the car a real-time 2D map of obstacles and open space. 

### Important Note
In our current code, we do not make use of the LiDAR, opting for a more straightforward approach for our first year. We already have a LiDAR and a stand, but we do not intend to utilize them.

---

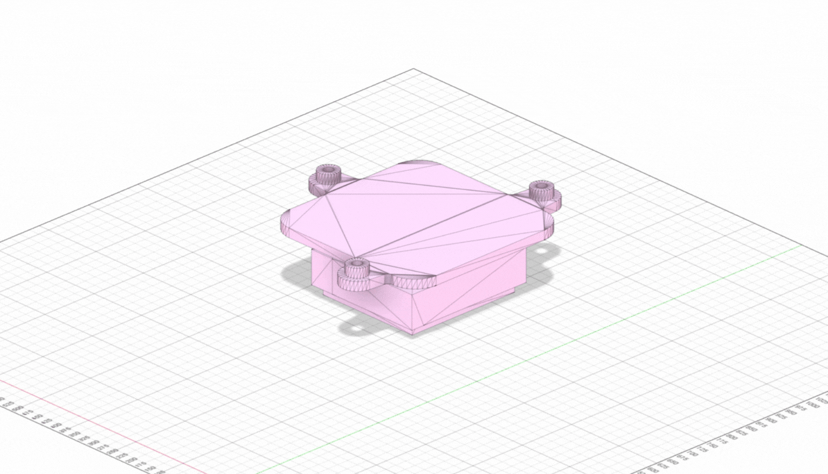
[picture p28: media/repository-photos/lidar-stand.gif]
|  |
|:--:|
| **Lidar Stand** |

</br>

---

</br>

# Software
## Frameworks
### Python 3.0
Python 3 is the core programming language used to build and run the autonomous car logic. Its simplicity, readability, and massive library pool make it ideal for controlling hardware like the Raspberry Pi. For robotics, Python makes it easy to interface with sensors and actuators, process images, and manage logic. However, Python is slower than compiled languages like C++, and because it’s dynamically typed, certain bugs may only appear at runtime if not carefully tested.

### ROS2 Humble 
ROS 2 (Robot Operating System 2) Humble is a modern, open-source robotics middleware designed to enable communication between nodes in robotic systems. It provides tools for message passing to aid with maximizing robot software efficiency. Although efficient, it is difficult and time-consuming to incorporate a working ROS2 environment into your code. It is for this reason that only the obstacle challenge uses ROS 2 while the open challenge is done with a standalone Python file.
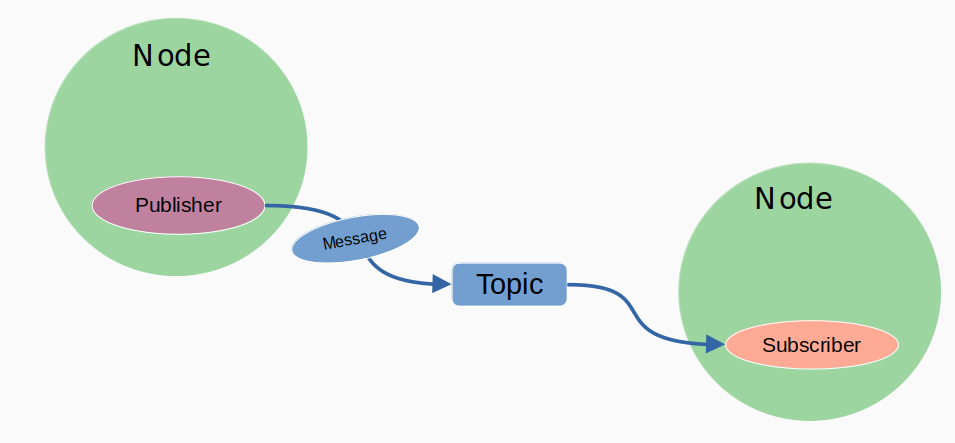
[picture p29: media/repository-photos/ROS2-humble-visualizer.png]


## Libraries
### Picamera2
Picamera2 is a library used to interface with the Raspberry Pi's camera module. It allows the robot to capture real-time photos and videos, which are critical for analyzing the robot environment. It provides full control over resolution, frame rate, and pixel format to effectively work in tandem with OpenCV.

### OpenCV
OpenCV (Open Source Computer Vision Library) is used to process camera frames, apply thresholding, and detect contours within specified regions of interests (ROIs). This data is used to determine the robot's orientation and distance relative to walls and pillars to guide its movement throughout the course.

### Cv_bridge
cv_bridge is a ROS 2 library that converts between ROS Image messages and OpenCV images, enabling image processing with OpenCV in ROS-based applications.

### Time
The built-in Python time module is used for time-based operations, such as delays (sleep) or measuring time elapsed since an event.

### Numpy
NumPy is a fundamental Python library for numerical computation. In robotics, it's often used for handling arrays, matrices, and mathematical operations efficiently. In our code, it is used for creating and handling arrays for color thresholding in HSV space.

### ROS_ROBOT_CONTROLLER_SDK
This custom Python SDK (Software Development Kit) provided by HiWonder is responsible for controlling robot hardware, including steering servos, throttle motors, and RGB LEDs. It turns low-level control into simple methods, allowing the main code to remain clean.

## Open Challenge
### Overview
The Open Challenge is designed to test a robot’s ability to autonomously navigate a closed-loop course using only the black walls as guidance. The robot must detect walls, align itself, make smooth turns at corners, and complete 3 laps without manual intervention in under 3 minutes. The main focus is on path-following and code accuracy.

#### Game Map
<table>
  <tr>
    <td style="border: 200px solid black; padding: 5px;">
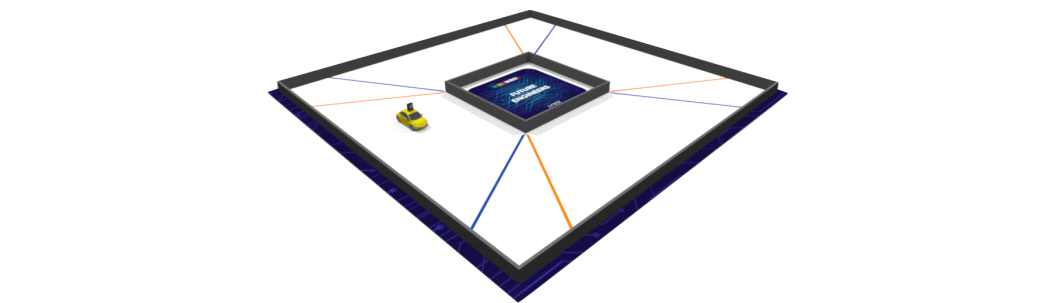
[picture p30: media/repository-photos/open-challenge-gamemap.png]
      
    </td>
  </tr>
</table>

### Difficulties
In the Open Challenge, the course can be set up in either a wide(100cm) or a narrow(60cm) configuration, and each comes with its own difficulties for vision and navigation. 
In the wide setup, the black walls are spaced much farther apart. This makes the robot’s region of interest (ROI) readings weaker because the walls occupy a smaller portion of the camera frame.
The narrow configuration creates the opposite problem. With the walls placed close together, the black regions fill a large portion of the ROIs, making the system very sensitive.

To be successful, the code must be consistent enough to be able to navigate through both scenarios, which each present conflicting issues. Fixing an error in the wide setup may break something in the narrow setup and vice versa.

### Our Solution
The primary means of navigation in the open challenge lies in the camera. The camera captures frames multiple times a second and performs wall following logic with information inside the ROIs. ROIs or region of interests are small rectangles placed strategically in areas of interest to perform wall detection. The open challenge includes 3 of these ROIs initialized at the top

The left and right ROIs are each placed on the edge of their respective sides. They are essential for the detection of differences in wall size to do PD steering and detect turn segments. 
The orange ROI is a thin rectangular box, centered near the bottom of the frame. It is used to detect the orange line on the ground, detecting turn areas for lap counting only.

In order to begin camera detection, we must define our ROIs, initialize the camera, and define the HSV ranges for orange:

```
picam2 = Picamera2()
picam2.preview_configuration.main.size = (640, 480)
picam2.preview_configuration.main.format = "RGB888"
picam2.preview_configuration.controls.FrameRate = 30
picam2.preview_configuration.align()
picam2.configure("preview")
picam2.start()
time.sleep(1)

lower_orange = np.array([5, 100, 100])
upper_orange = np.array([20, 255, 255])

# ---- Define ROIs ----
left_roi = (0, 200, 180, 180) # x, y, w, l
right_roi = (460, 200, 180, 180)
orange_roi = (100, 360, 440, 40) 
```   

Wait for button press with ROS2 threading before starting.
```
def listen_to_button_events():
    command = 'source /home/ubuntu/.zshrc && ros2 topic echo /ros_robot_controller/button'
    process = subprocess.Popen(
        ['docker', 'exec', '-u', 'ubuntu', '-w', '/home/ubuntu', 'MentorPi', '/bin/zsh', '-c', command],
        stdout=subprocess.PIPE,
        stderr=subprocess.PIPE,
        text=True
    )

    while True:
        output = process.stdout.readline()
        if output:
            line = output.strip()
            if line.startswith("id:"):
                button_id = int(line.split(":")[1].strip())
            elif line.startswith("state:"):
                state = int(line.split(":")[1].strip())
                if state == 1 and button_id == 2:
                    print(f"Button {button_id} pressed")
                    return button_id
        time.sleep(0.1)
        
def check_node_status():
    command = 'source /home/ubuntu/.zshrc && ros2 topic list'
    result = subprocess.run(['docker', 'exec', '-u', 'ubuntu', '-w', '/home/ubuntu', 'MentorPi', '/bin/zsh', '-c', command], capture_output=True, text=True)
    return '/ros_robot_controller/button' in result.stdout

def wait_for_button_press():
    """Wait for button press using Docker ROS2 or fallback"""
    print("Waiting for button press to start...")
    
    # Check if ROS2 node is available
    while True:
        if check_node_status():
            print("ROS2 node detected")
            board.set_rgb([[1, 255, 0, 0], [2, 255, 0, 0]])
            button_id = listen_to_button_events()
            print(f"Button {button_id} pressed! Starting challenge...")
            return True

wait_for_button_press()
```

Now, we can apply masks, crop ROIs, and count pixels for navigation.

```
# ---- Get camera frame ----
frame = picam2.capture_array()
x, y, w, h = orange_roi
roi_crop = frame[y:y+h, x:x+w]

# Convert to HSV for color detection
hsv = cv2.cvtColor(roi_crop, cv2.COLOR_BGR2HSV)
mask_orange = cv2.inRange(hsv, lower_orange, upper_orange)

# Count orange pixels
orange_pixel_count = cv2.countNonZero(mask_orange)

if orange_pixel_count >= 500:  
    current_time = time.time()
    if current_time - last_orange_time > orange_cooldown:
        turns += 1

# Thresholding
gray = cv2.cvtColor(frame, cv2.COLOR_BGR2GRAY)
_, thresh = cv2.threshold(gray, 110, 255, cv2.THRESH_BINARY_INV)

mask = np.zeros_like(thresh)
cv2.rectangle(mask, (left_roi[0], left_roi[1]), (left_roi[0]+left_roi[2], left_roi[1]+left_roi[3]), 255, -1)
cv2.rectangle(mask, (right_roi[0], right_roi[1]), (right_roi[0]+right_roi[2], right_roi[1]+right_roi[3]), 255, -1)
masked = cv2.bitwise_and(thresh, mask)

contours, _ = cv2.findContours(masked, cv2.RETR_EXTERNAL, cv2.CHAIN_APPROX_SIMPLE)

# Crop ROIs
left_crop = thresh[left_roi[1]:left_roi[1]+left_roi[3], left_roi[0]:left_roi[0]+left_roi[2]]
right_crop = thresh[right_roi[1]:right_roi[1]+right_roi[3], right_roi[0]:right_roi[0]+right_roi[2]]

# Count black pixels
left_area = cv2.countNonZero(left_crop)
right_area = cv2.countNonZero(right_crop)
```

The purpose of this code is the generate us 3 pieces of information: amount of black pixels in the left roi, the amount of black pixels in the right roi, and the number of orange pixels in the orange roi. We can then use this information to steer our robot and count turns.

### PD Steering
Most of the time, the robot will be in a straight section where it will use PD steering to avoid walls. PD steering is a system used to correct the robot's movements so that it is centered between the two walls. 

The proportional term(P) is simply how far off you are from the center.
You compute an error with:
```
error = right_area - left_area
```
If the robot sees more black on the right, the error is positive, steer left.
If it sees more black on the left, the error is negative, steer right.

Then you apply:
```
steering = straight_pwm + kp * error
```
Where kp is a constant gain. This makes the robot steer proportionally to how far it’s off-center.

The derivative term looks at how fast the error is changing.
If the error is quickly swinging, it means the robot is wobbling. The derivative dampens this by applying a correction against sudden changes:
```
derivative = error - prev_error
steering += kd * derivative
```

where kd is another constant.
This helps smooth out steering and prevents oscillation (zig-zagging).

Our code utilizes PD steering like this.
```
area_diff = right_area - left_area
angle_pwm = int(STRAIGHT_PWM + area_diff * KP + (area_diff - prev_diff) * KD)
```
Here:
area_diff = error.
straight_pwm = neutral steering.
kp = how much to react to a error.
kd = how much to stabilize a change in turning angle
(area_diff - prev_diff) is the derivative.

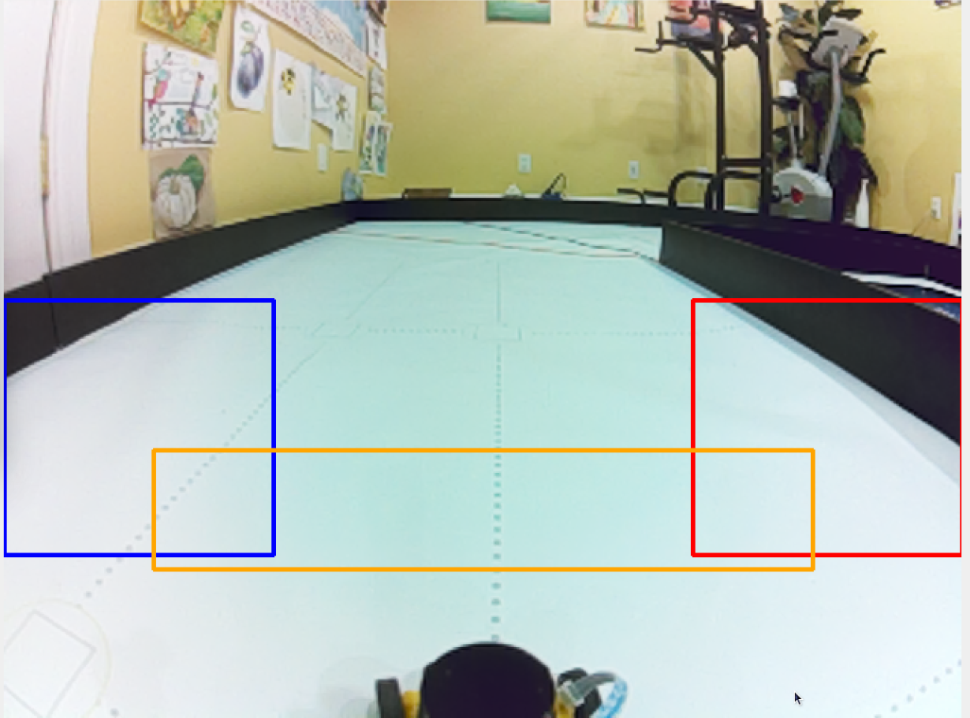
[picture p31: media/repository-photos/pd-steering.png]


Then we apply a clamp to make sure the steering angle never exceeds the predefined maximums and minimums
```
angle_pwm = max(min(angle_pwm, MAX_LEFT), MAX_RIGHT)
```
We need to apply the clamp to make sure the steering angle does not surpass the predefined maximums.

The car will continue running this code in a while loop until it detects 12 orange lines. Once it does, it will continue driving for a set amount of time before stopping:
```
if turns == 12: 
    stop_time = time.time()
    turns += 1
if turns >= 13:
    current_time = time.time()
    if current_time - stop_time >= 5:
        board.pwm_servo_set_position(0.1, [[4, 1500], [2, 1500]])
        lap_complete = True
```
#### Pre-Turn
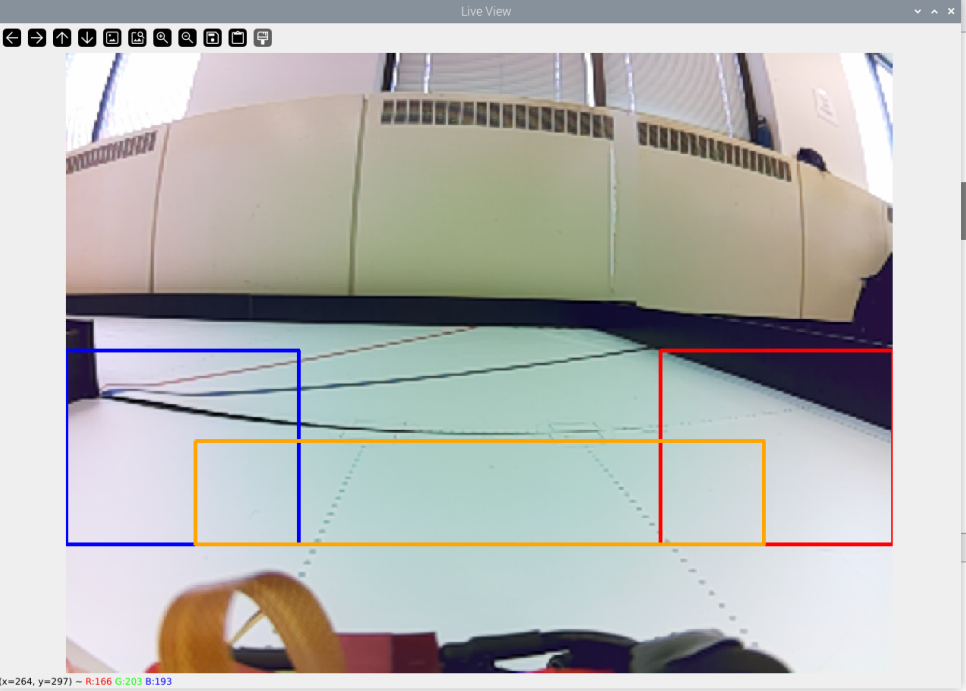
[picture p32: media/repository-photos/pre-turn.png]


#### Post-Turn
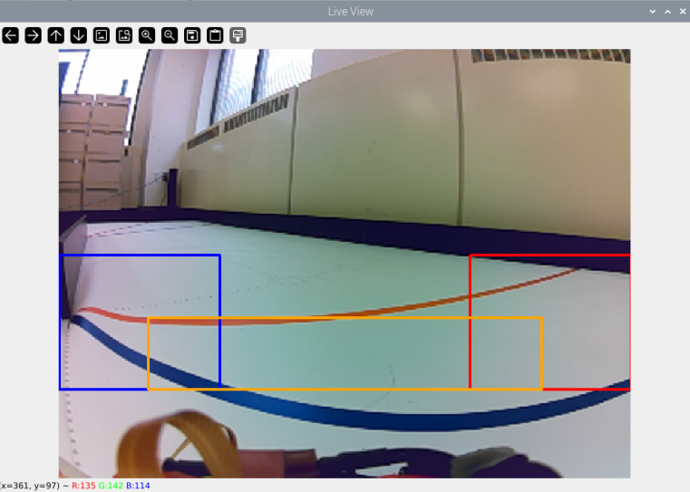
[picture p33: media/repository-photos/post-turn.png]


## Obstacle Challenge

### Overview
The obstacle challenge is a much more difficult version of the open challenge. In this challenge, there are red and green traffic pillars that the car must navigate around, as well as a parking lot. A red pillar indicates that the car should turn right to pass the pillar, and a green pillar indicates a left turn to pass the pillar. The car starts in a straight section or parking lot (for extra points) and must navigate 3 laps around the track avoiding obstacles. Once the 3 laps are finished the car can perform a difficult parallel parking maneuver for additional points. The parking lot is 1.5x the length of the car. In our case the parking lot will be about 24.5cm.

#### Game Map
<table>
  <tr>
    <td style="border: 200px solid black; padding: 5px;">
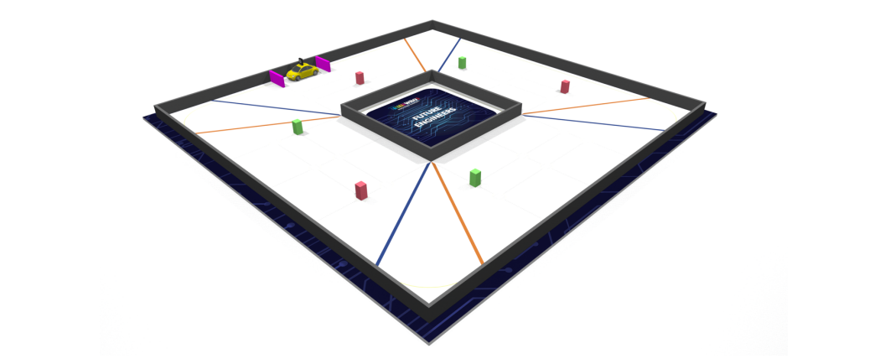
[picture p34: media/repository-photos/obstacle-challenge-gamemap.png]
      
    </td>
  </tr>
</table>

### Difficulties
The obstacle challenge presents many difficult challenges that build onto the open challenge. Although the walls are set at 100cm, steering around the pillar while avoiding walls and detecting turns is difficult to do consistently. 
In order to perform a parallel park the information and car movements must be very precise since the parking lot is only 1.5x the cars size.

### Our Solution
Unlike our open challenge, we used ROS 2 for our obstacle challenge, providing speed and reliability. Another reason comes from the complex nature of the challenge. That is why our strategy involves multiple sensors inputs (camera, imu) and several behaviours (park, navigate). Doing all of this in a single Python script would be slower, harder to maintain, and harder to debug. ROS 2 allows us to use multiple Python scripts (nodes) to communicate to one another with topics. The following is a visualization of the workspace containing all the packages required for ROS 2 to run.
```
~/fe_ws/src/obstacle_challenge/
├── obstacle_challenge/
│   ├── __init__.py
│   ├── camera_node.py
│   ├── imu_node.py
│   ├── navigator_node.py
│   └── ros_robot_controller_sdk.py
├── launch/
│   └── obstacle_challenge_launch.py
├── package.xml
└── setup.py
```

This is a visualziation of how the nodes communicate:
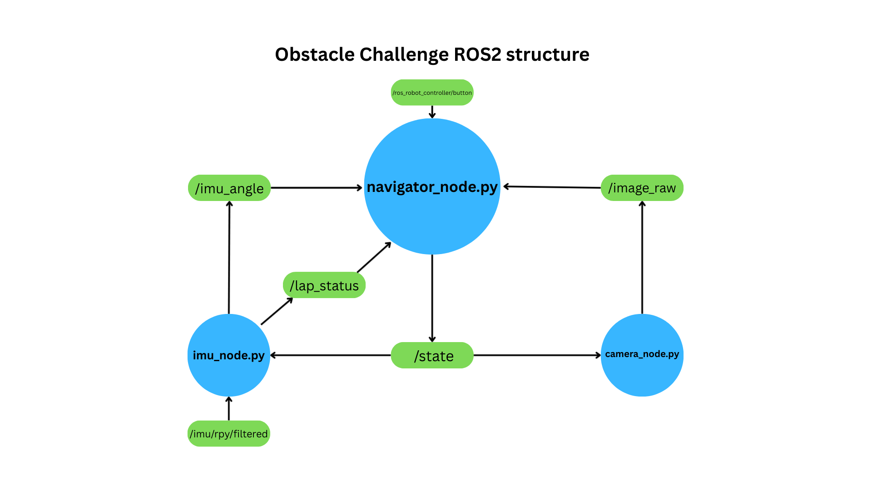
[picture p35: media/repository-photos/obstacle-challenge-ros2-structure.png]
NAVIGATOR_NODE py


### NODES/TOPICS
#### navigator_node.py
- Core decision making node
- Subscribes to /image_raw from camera_node.py
- Subscribes to /imu_angle from imu_node.py
- Subscribes to /lap_status from imu_node.py
- Subscribes to /ros_robot_controller/button
- Publishes to /state to communicate to other nodes
  Combines camera and IMU data to output driving decisions (turning, avoiding, lap counting, parking).

#### camera_node.py
- Captures frames from the Raspberry Pi's camera
- Subscribes to /state to know what to do
- Publishes to /image_raw to transmit camera information
  Provides visual input for pillar and wall detection

#### imu_node.py
- Reads IMU sensor value and transmits important information
- Subscribes to /imu/rpy/filtered for filtered IMU data
- Publishes to /imu_angle to transmit current IMU angle
- Publishes to /lap_status to transmit lap information
  Provides orientational information for lap counting and navigation

#### ROS2
In short:
navigator_node.py: The brain of the challenge

camera_node.py: The eyes of the challenge

imu_node.py: Balance and lap counting

We like to think of our navigator node as a multi-state machine. It has 5 drive states and 3 pillar states. The 5 drive states are as follows:
1. Button: Wait for button press before starting.
2. Start: Escape from parking lot.
3. Navigate: The main part of challenge, navigate 3 laps around the track.
4. Park: Go into the parking lot.
5. Stop: Stop all movement and nodes.

Since the navigator node is the main for controlling the robot, it must communicate with the other nodes with subscribers and publishers to coordinate current drive and button states.
```
self.create_subscription(Image, '/image_raw', self.camera_callback, 10)
self.create_subscription(Float32, '/imu_angle', self.imu_callback, 10)
self.create_subscription(ButtonState, '/ros_robot_controller/button', self.button_callback, 10)
self.stat_pub = self.create_publisher(String, '/state', 10)
```

#### Camera logic
ROI visualization
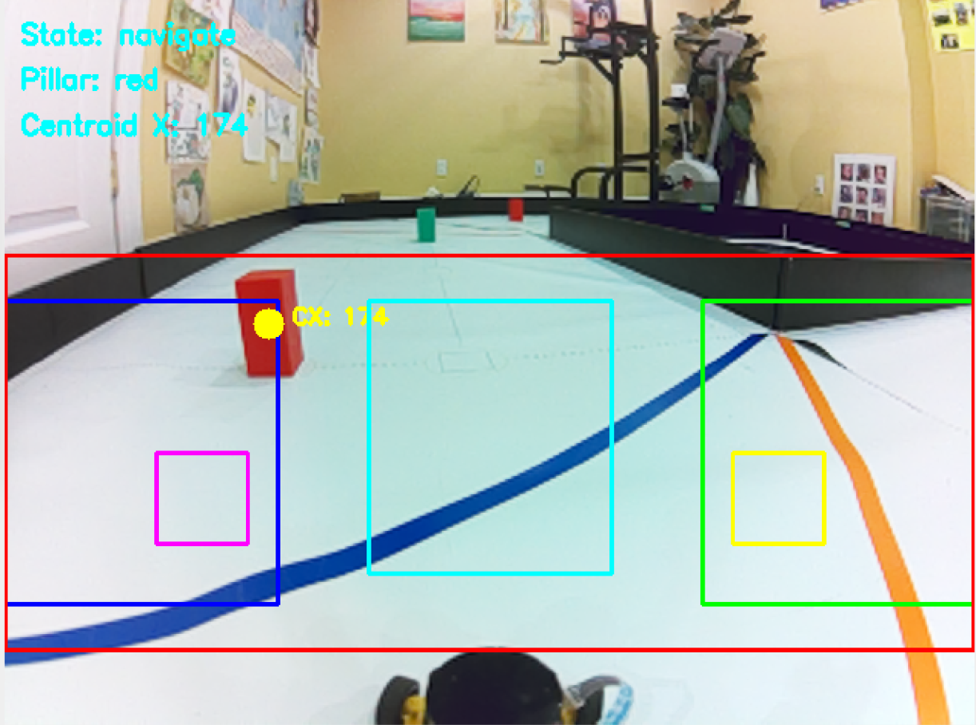
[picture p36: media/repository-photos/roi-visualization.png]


The camera logic is largely the same, with the addition of the central ROI and colour detecting HSV ranges.
```
self.lower_red1 = np.array([0, 120, 50])
self.upper_red1 = np.array([5, 255, 255])
self.lower_red2 = np.array([175, 120, 50])
self.upper_red2 = np.array([179, 255, 255])
self.lower_green = np.array([50, 150, 80])
self.upper_green = np.array([95, 255, 255])

self.lower_magenta = np.array([150, 100, 80])
self.upper_magenta = np.array([170, 255, 255])

self.lower_orange = np.array([5, 100, 100])
self.upper_orange = np.array([20, 255, 255])
```

The camera node's job is to publish raw coloured frames to the navigator node in order for it to perform turns.
```
def publish_frame(self):
    frame = self.picam2.capture_array()
        msg = self.bridge.cv2_to_imgmsg(frame, encoding='rgb8')
        self.publisher.publish(msg)
```
The navigator node receives these frames and performs the same logic as the open challenge for black pixels. For the coloured pixels, it performs cropping to focus on a particular ROI, and colour masking to isolate specific pixels. Then the pixels are counted to be used for steering logic.
```
    
gray = cv2.cvtColor(frame, cv2.COLOR_RGB2GRAY)
_, thresh = cv2.threshold(gray, 110, 255, cv2.THRESH_BINARY_INV)

left_crop = thresh[self.left_roi[1]:self.left_roi[1]+self.left_roi[3], 
                   self.left_roi[0]:self.left_roi[0]+self.left_roi[2]]
right_crop = thresh[self.right_roi[1]:self.right_roi[1]+self.right_roi[3], 
                   self.right_roi[0]:self.right_roi[0]+self.right_roi[2]]
front_wall_crop = thresh[self.front_wall_roi[1]:self.front_wall_roi[1]+self.front_wall_roi[3], 
                  self.front_wall_roi[0]:self.front_wall_roi[0]+self.front_wall_roi[2]]
left_wall_crop = thresh[self.left_wall_roi[1]:self.left_wall_roi[1]+self.left_wall_roi[3], 
                   self.left_wall_roi[0]:self.left_wall_roi[0]+self.left_wall_roi[2]]
right_wall_crop = thresh[self.right_wall_roi[1]:self.right_wall_roi[1]+self.right_wall_roi[3], 
                   self.right_wall_roi[0]:self.right_wall_roi[0]+self.right_wall_roi[2]]
center_color_crop = frame[self.center_roi[1]:self.center_roi[1]+self.center_roi[3], 
                   self.center_roi[0]:self.center_roi[0]+self.center_roi[2]]

self.left_area = cv2.countNonZero(left_crop)
self.right_area = cv2.countNonZero(right_crop)
#pillar steering
self.front_wall_area = cv2.countNonZero(front_wall_crop)
self.left_wall_area = cv2.countNonZero(left_wall_crop)
self.right_wall_area = cv2.countNonZero(right_wall_crop)

hsv_center = cv2.cvtColor(center_color_crop, cv2.COLOR_RGB2HSV)

center_magenta_mask = cv2.inRange(hsv_center, self.lower_magenta, self.upper_magenta)
center_orange_mask = cv2.inRange(hsv_center, self.lower_orange, self.upper_orange)
       
center_green_mask = cv2.inRange(hsv_center, self.lower_green, self.upper_green)
center_red_mask = cv2.bitwise_or(cv2.inRange(hsv_center, self.lower_red1, self.upper_red1), 
                       cv2.inRange(hsv_center, self.lower_red2, self.upper_red2))
center_red_mask = cv2.subtract(center_red_mask, center_magenta_mask)
center_red_mask = cv2.subtract(center_red_mask, center_orange_mask)

# Count pixels
self.center_magenta_area = cv2.countNonZero(center_magenta_mask)
self.center_green_area = cv2.countNonZero(center_green_mask)
self.center_red_area = cv2.countNonZero(center_red_mask)
```

#### Parking lot escape
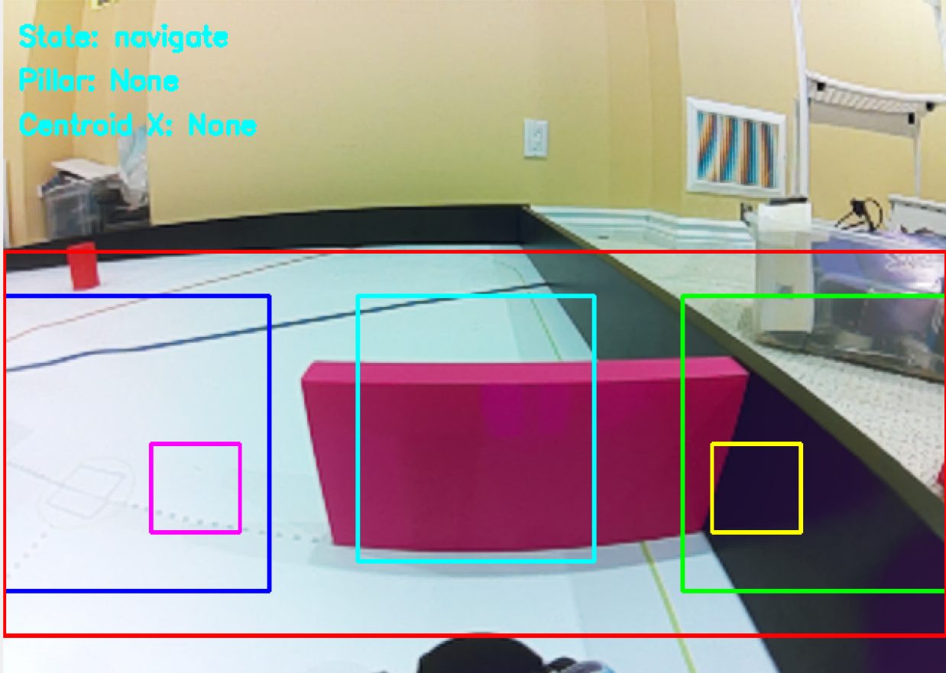
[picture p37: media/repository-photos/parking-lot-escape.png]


In order to escape the parking lot, we must determine which side the car is on. We can do this by comparing the number of black pixels in the left roi with the right roi.
```
if self.mode == "start" and self.parking_side is None:
   if self.left_area > self.right_area:
       self.parking_side = "left"
   elif self.right_area > self.left_area:
       self.parking_side = "right" 
```
```
if self.parking_side == "left": #wall is to the left
  #1
  self.board.pwm_servo_set_position(0.1, [[2, 1570]])
  self.board.pwm_servo_set_position(0.1, [[4, self.max_right]])
  time.sleep(2.3)
  #2
  self.board.pwm_servo_set_position(0.1, [[2, 1420]])
  self.board.pwm_servo_set_position(0.1, [[4, self.max_left]])
  time.sleep(2.3)
  #3
  self.board.pwm_servo_set_position(0.1, [[2, 1570]])
  self.board.pwm_servo_set_position(0.1, [[4, self.max_right]])
  time.sleep(2.3)
  #4
  self.board.pwm_servo_set_position(0.1, [[2, 1420]])
  self.board.pwm_servo_set_position(0.1, [[4, self.max_left]])
  time.sleep(2.3)
  #5
  self.board.pwm_servo_set_position(0.1, [[2, 1420]])
  self.board.pwm_servo_set_position(0.1, [[4, self.max_left]])

else: #wall is to the right
  #1
  self.board.pwm_servo_set_position(0.1, [[2, 1570]])
  self.board.pwm_servo_set_position(0.1, [[4, self.max_left]])
  time.sleep(2.3)
  #2
  self.board.pwm_servo_set_position(0.1, [[2, 1420]])
  self.board.pwm_servo_set_position(0.1, [[4, self.max_right]])
  time.sleep(2.3)
  #3
  self.board.pwm_servo_set_position(0.1, [[2, 1570]])
  self.board.pwm_servo_set_position(0.1, [[4, self.max_left]])
  time.sleep(2.3)
  #4
  self.board.pwm_servo_set_position(0.1, [[2, 1420]])
  self.board.pwm_servo_set_position(0.1, [[4, self.max_right]])
  time.sleep(2.3)               
self.mode = "navigate"
```
Based on which side the car starts on, it will execute a series of precise servo movements before backing up to begin the navigation.
#### Pillar detection/Navigation
If the center ROI sees enough pixels of red/green it will stop PD steering and enter the corresponding pillar mode.

```
if self.center_red_area > self.pillar_detection_thresh and self.center_red_area > self.center_green_area:
   self.pillar_mode = "red"
   self.prev_pillar_error = self.center_red_area
   
elif self.center_green_area > self.pillar_detection_thresh and self.center_green_area > self.center_red_area:
   self.pillar_mode = "green"  
   self.prev_pillar_error = self.center_green_area

else:
   #Exit condition
   current_pillar_area = self.center_red_area if self.pillar_mode == "red" else self.center_green_area
   # Use hysteresis to prevent flickering
   if (current_pillar_area < self.pillar_clear_thresh and 
       current_time - self.last_pillar_time > 0.1 and self.pillar_mode is not None):  # Wait 0.5s of low signal
       self.pillar_mode = None
```
For a more accurate estimation of the pillars' location, we must find the x-value of the pillar centroid while the y-value is used for debugging.

```
self.pillar_cx = None  # Reset centroid each frame
self.pillar_cy = None

if self.pillar_mode == "red":
   # Find centroid
   M = cv2.moments(center_red_mask)
   if M["m00"] > 0:
       self.pillar_cx = int(M["m10"] / M["m00"])
       self.pillar_cy = int(M["m01"] / M["m00"])
       self.pillar_cy = self.pillar_cy + self.center_roi[1]

elif self.pillar_mode == "green":
   # Find centroid
   M = cv2.moments(center_green_mask)
   if M["m00"] > 0:
       self.pillar_cx = int(M["m10"] / M["m00"])
       self.pillar_cy = int(M["m01"] / M["m00"])
       self.pillar_cy = self.pillar_cy + self.center_roi[1]
```

You may have also noticed the 3 additional wall rois
```
self.front_wall_roi = (260, 200, 160, 180)    # Upper center for front walls
self.left_wall_roi = (100, 300, 60, 60)     # Left side walls
self.right_wall_roi = (480, 300, 60, 60)   # Right side walls
```
These ROIs are used to prevent hitting a wall in certain cases, primarily if a wall is between the car and a pillar or if the pillar is placed at a 90 degree turning section. The front_wall_roi will detect black in front of the car and trigger a harsh turn according to the pillar colour. Similarly if enough black is detected in the left or right wall roi it will turn the other direction. 
```
#emergency turns within pillar steering logic.
if self.wall_in_front or self.right_wall_close:
   self.angle_pwm = self.max_left
if self.wall_in_front or self.left_wall_close:
   self.angle_pwm = self.max_right
```
#### Steering logic
When a red pillar is in the center-right area we must turn right to pass the pillar on the right side. When the pillar is on the left side we can turn slightly to the left to make sure we don't overshoot. Similarly for the green pillars, when the green pilar is on the center-left we must turn left to pass the pillar on the left side and turn right otherwise.
With the x-value of the centroid value we can execute this logic with the following formula where 225 is how far left or right from the center of the screen to change turning directions.

```
if self.pillar_cx is not None:  
    if self.pillar_mode == "red":
        error = self.pillar_cx - self.screen_center_x + 225
        steering_adjustment = -error * 1.5  
        self.angle_pwm = self.straight_pwm + steering_adjustment
        
    elif self.pillar_mode == "green":
        error = self.pillar_cx - self.screen_center_x - 225
        steering_adjustment = -error * 1.5
        self.angle_pwm = self.straight_pwm + steering_adjustment
```

In the image below the X value of the pillar centroid is 174
In this frame the pillar is not yet far enough left for the car to turn left. If the formula is correct it should be turning right to avoid the pillar.

We plug in 174 into the formula
error = 174 - 320 - 225
error = 79
And since steering adjustment = -error * 1.5
steering adjustment = -118.5
Therefore the final turning pwm is 1381.5 which corresponds to a left turn.

In this next case the X value of the pillar centroid is 30

Now, the pillar is far enough left to safely execute a left turn.
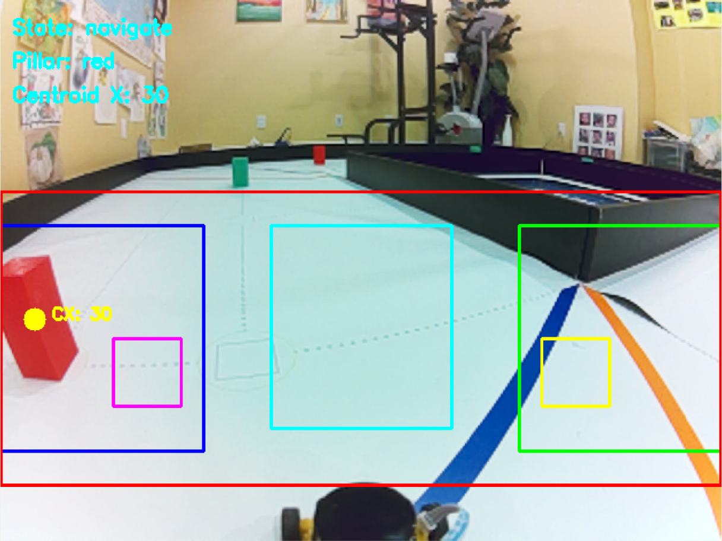
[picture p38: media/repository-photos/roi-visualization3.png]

We plug in 30 into the formula
error = 30 - 320 - 225
error = -65
And since steering adjustment = -error * 1.5
steering adjustment = 97.5
Therefore the final turning pwm is 1597.5 which corresponds to a slight left turn

Since pillar steering has a higher priority in our code, we will be using pillar steering for a large majority of the challenge. In straight/turn sections where no pillars are detected, it will default to the same PD steering logic used in the open challenge.
```
if self.pillar_cx is not None: # Pillar steering if pillar is detected
#pillar logic here
else: # PD steering if no pillar is detected
    area_diff = self.right_area - self.left_area
    self.angle_pwm = int(self.straight_pwm + area_diff * self.kp + (area_diff - self.prev_diff) * self.kd)
    self.angle_pwm = max(min(self.angle_pwm, self.max_left), self.max_right)
    self.prev_diff = area_diff
```
            
Once 3 laps of navigation have been complete, the imu node sends the stop command to the navigator node.

```
if self.lap_count >= 3:
    msg_out = Bool()
    msg_out.data = True
    self.lap_done_pub.publish(msg_out)
    self.get_logger().info("3 laps done!")
```
Once the navigator node receives this information it will change it's state and prepare for parking.
```
def lap_callback(self, msg):
    if msg.data and self.state != "park":
        self.get_logger().info("Received IMU signal: 3 laps complete, switching to parking mode.")
        self.state = "park"
        self.lap_done_time = time.time()
```

#### Parking
At the end of the final lap, the car will keep avoiding obstacles as normal until the parking lot gets close. Once the parking lot is visible in the camera frame, we can swerve into it to complete partial parking.
```
if parking_cx is not None and self.mode == "park":
  if self.parking_side = "right"
      self.board.pwm_servo_set_position(0.1, [[4, 1300]]) 
      self.board.pwm_servo_set_position(0.1, [[2, 1560]])  
      time.sleep(2.0) 
  else:
      self.board.pwm_servo_set_position(0.1, [[4, 1700]]) 
      self.board.pwm_servo_set_position(0.1, [[2, 1560]])  
      time.sleep(2.0)  
  
      self.board.pwm_servo_set_position(0.1, [[4, 1500]]) 
      self.board.pwm_servo_set_position(0.1, [[2, 1560]])  
      time.sleep(1.5)
  
      self.board.pwm_servo_set_position(0.1, [[2, 1500]])
```
## Image Resources

<p><strong>Lidar:</strong> <a href="https://botland.store/laser-scanners-lidar/21991-d500-lidar-kit-stl-19p-laser-scanner-360-degrees-12m-dfrobot-sen0547-6959420922680.html" target="_blank">Click Here</a></p>
<p><strong>WRO Future Engineers Map:</strong> <a href="https://world-robot-olympiad-association.github.io/future-engineers-gs/" target="_blank">Click Here</a></p>
<p><strong>Gens Ace 1300 mAh LiPo Battery:</strong> <a href="https://www.horizonhobby.com/product/7.4v-1300mah-2s-45c-g-tech-smart-lipo-battery-deans/GEA132S45DGT.html" target="_blank">Click Here</a></p>
<p><strong>Wheels:</strong> <a href="https://www.amazon.ca/Abendor-Spoke-Narrow-Aluminum-Wltoys/dp/B09ZYVGYB4?th=1" target="_blank">Click Here</a></p>
<p><strong>Furitek Micro Komodo Motor:</strong> <a href="https://furitek.com/products/furitek-micro-komodo-brushless-motor" target="_blank">Click Here</a></p>
<p><strong>Furitek Lizard Pro ESC:</strong> <a href="https://www.ebay.ca/itm/375134202747" target="_blank">Click Here</a></p>
<p><strong>HS-5055MG Servo:</strong> <a href="http://hitecrcd.com/hs-5055mg-economy-metal-gear-feather-servo/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" target="_blank">Click Here</a></p>
<p><strong>5/Zero Camera:</strong> <a href="https://www.amazon.ca/Raspberry-Camera-Module-OV5647-Sensor/dp/B0D324RKRZ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" target="_blank">Click Here</a></p>
<p><strong>MPU-6050 6-Axis IMU:</strong> <a href="https://www.researchgate.net/figure/MPU6050-MPU6050-sensor-module-is-complete-6-axis-Motion-Tracking-Device-It-combines_fig2_366214205" target="_blank">Click Here</a></p>
<p><strong>Open and Obstacle Challenge Mats (Page 6 and 10):</strong> <a href="https://wro-association.org/wp-content/uploads/WRO-2025-Future-Engineers-Self-Driving-Cars-General-Rules.pdf" target="_blank">Click Here</a></p>

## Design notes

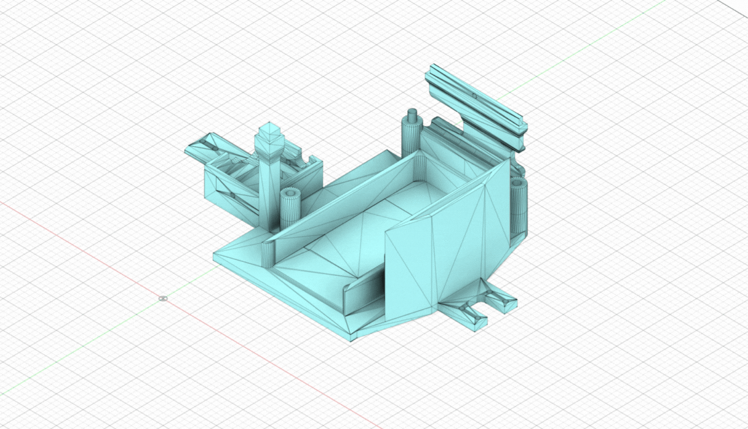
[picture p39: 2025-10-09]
media/repository-photos/bottom-chassis.gif

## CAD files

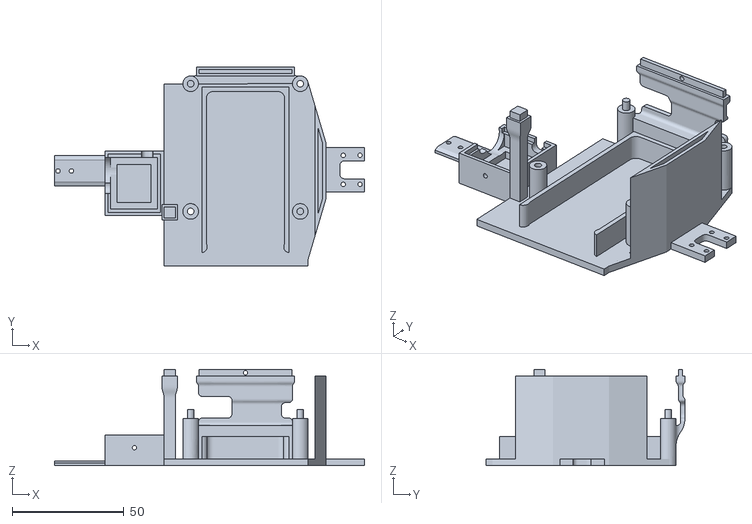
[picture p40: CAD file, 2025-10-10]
3d-models/chassis-bottom.stl
138.6 x 89.0 x 43.0

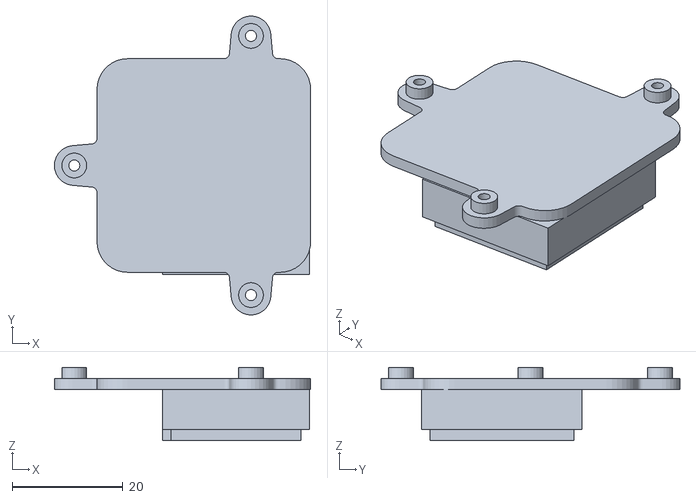
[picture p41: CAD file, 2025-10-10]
3d-models/lidar-stand.stl
46.3 x 54.0 x 13.2

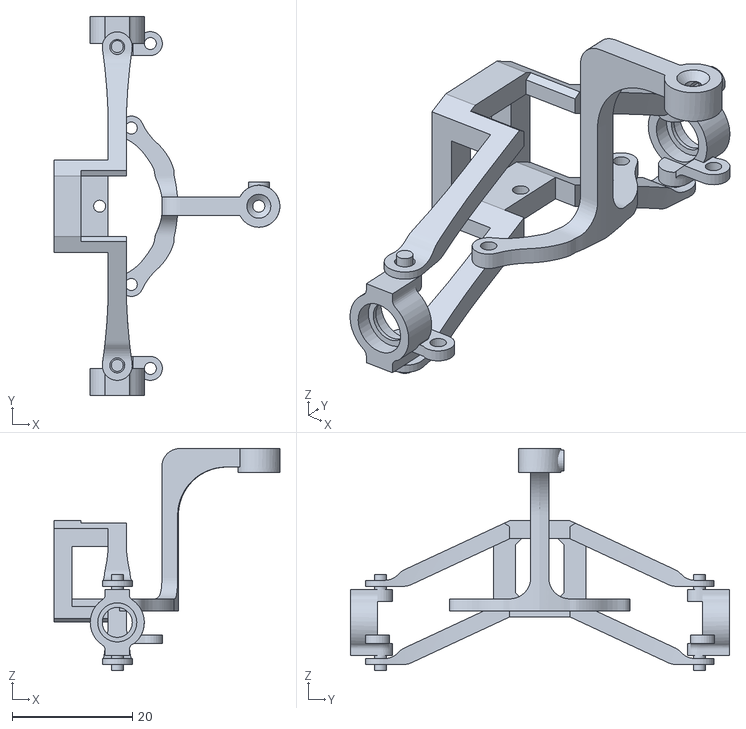
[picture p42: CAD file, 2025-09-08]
other/Turning System STL.stl
37.5 x 63.0 x 36.9

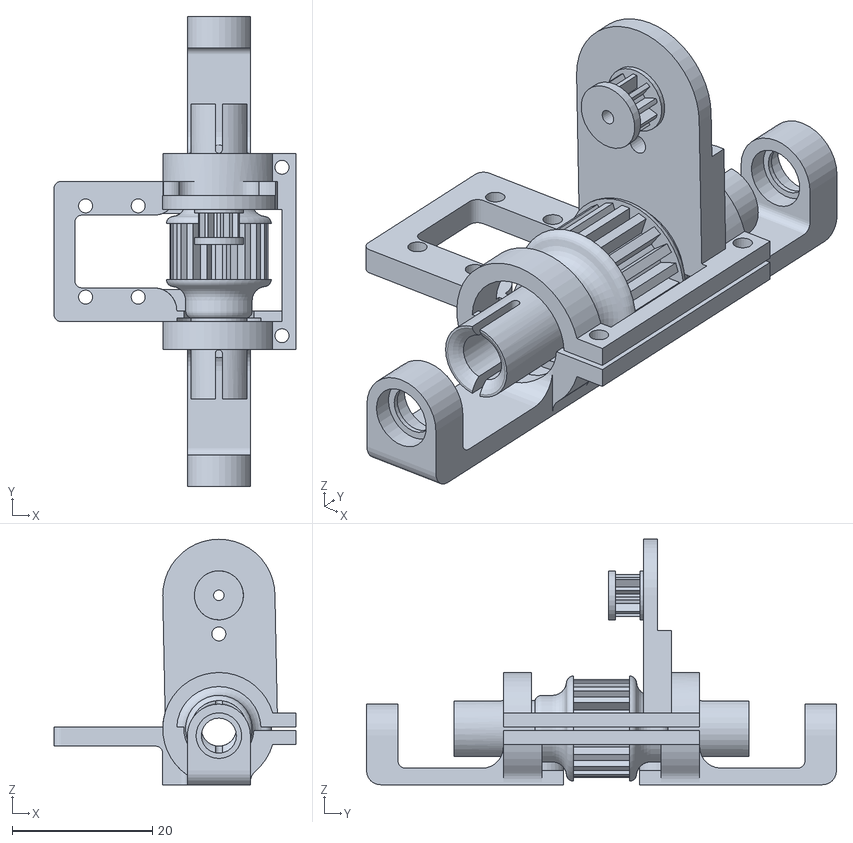
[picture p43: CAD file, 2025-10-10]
3d-models/motor-mechanism.stl
34.5 x 67.0 x 35.0

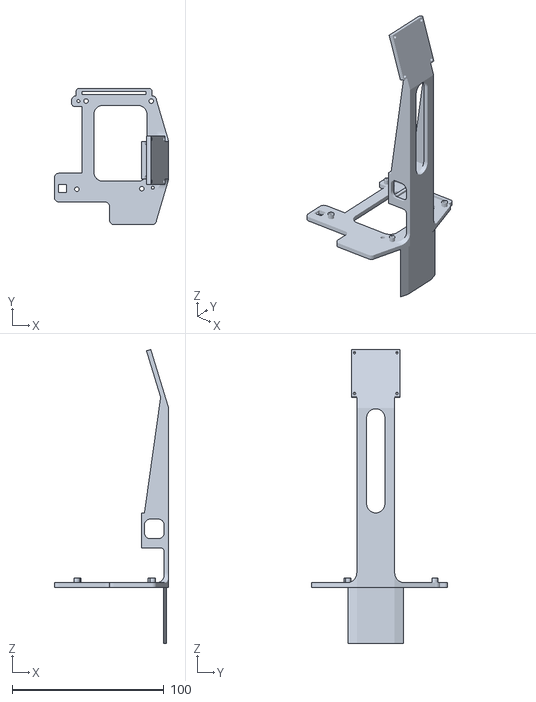
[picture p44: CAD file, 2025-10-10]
3d-models/chassis-top.stl
75.4 x 89.9 x 193.8

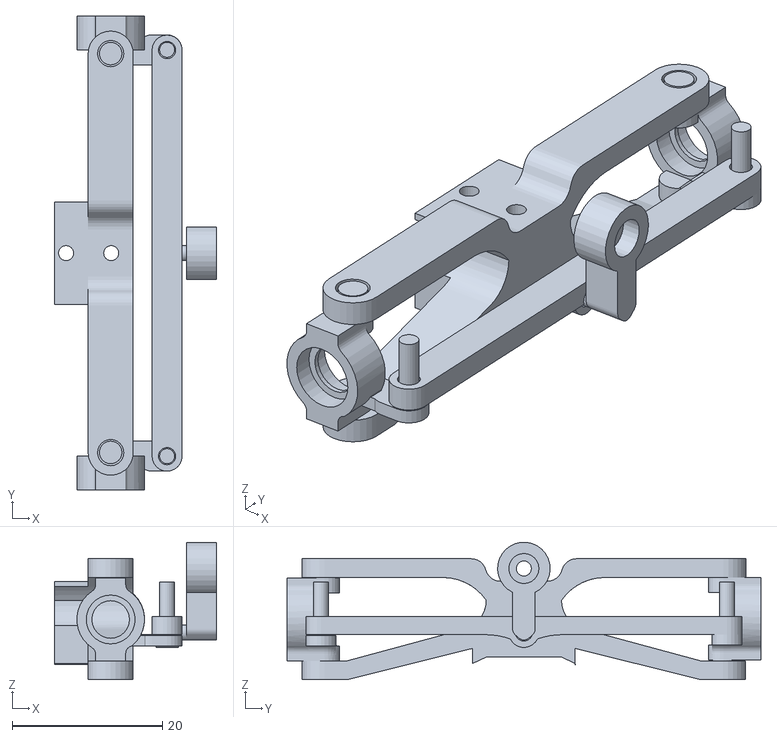
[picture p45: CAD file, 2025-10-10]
3d-models/steering-system.stl
21.6 x 63.0 x 18.3

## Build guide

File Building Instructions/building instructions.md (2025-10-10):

## Building Instructions

#### GIF of Instructions
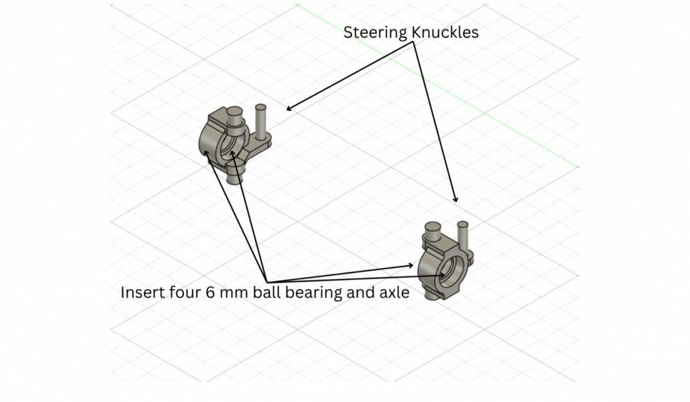
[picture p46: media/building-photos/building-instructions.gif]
|  |
|:--:|
| *See Full Instructions Below* |

### Step 1 — Steering knuckles: add bearings
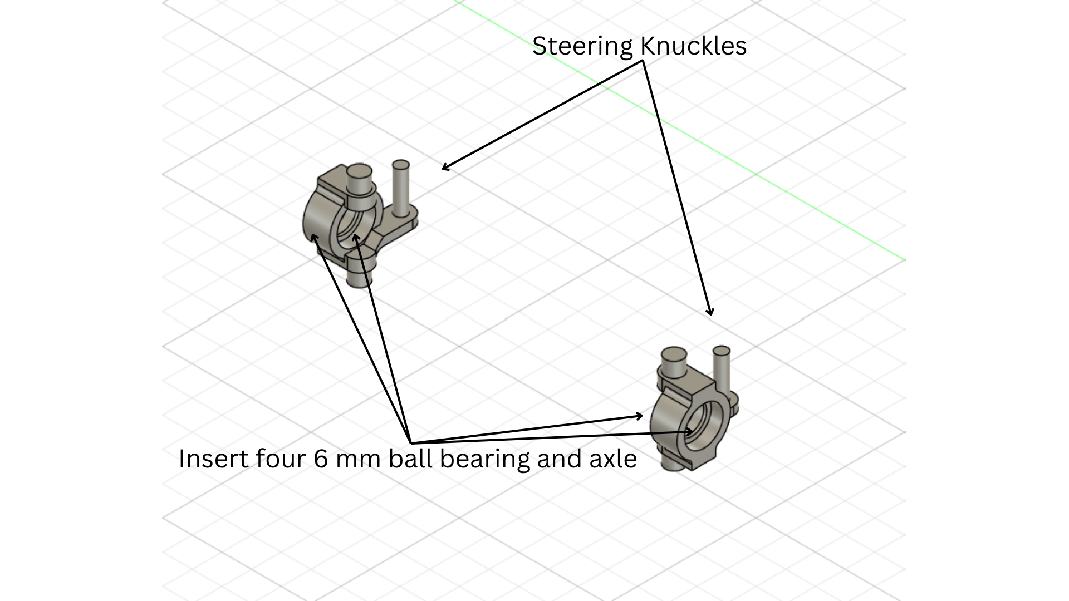
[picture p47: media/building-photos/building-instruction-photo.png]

Insert four 6 mm ball bearings and axles.

---

### Step 2 — Prep for wheels
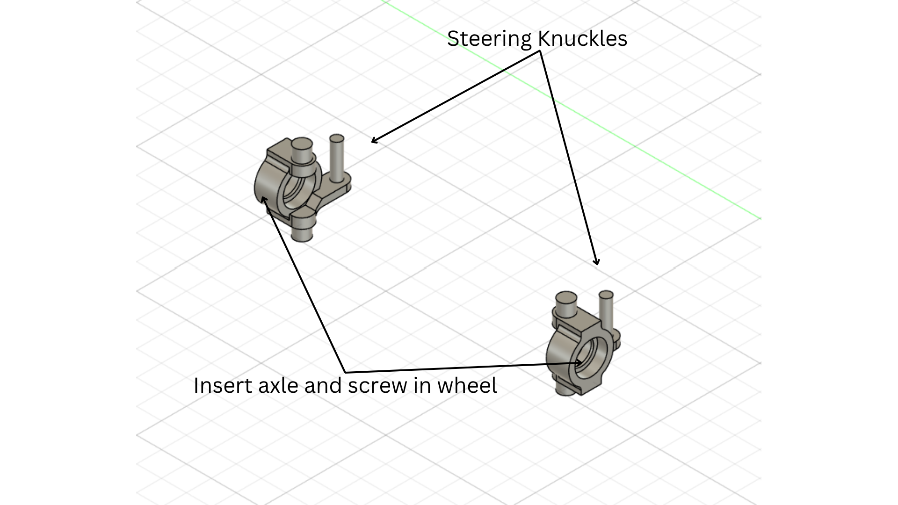
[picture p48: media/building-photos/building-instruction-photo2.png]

Insert axle and screw in wheel.

---

### Step 3 — Link knuckles to control arm
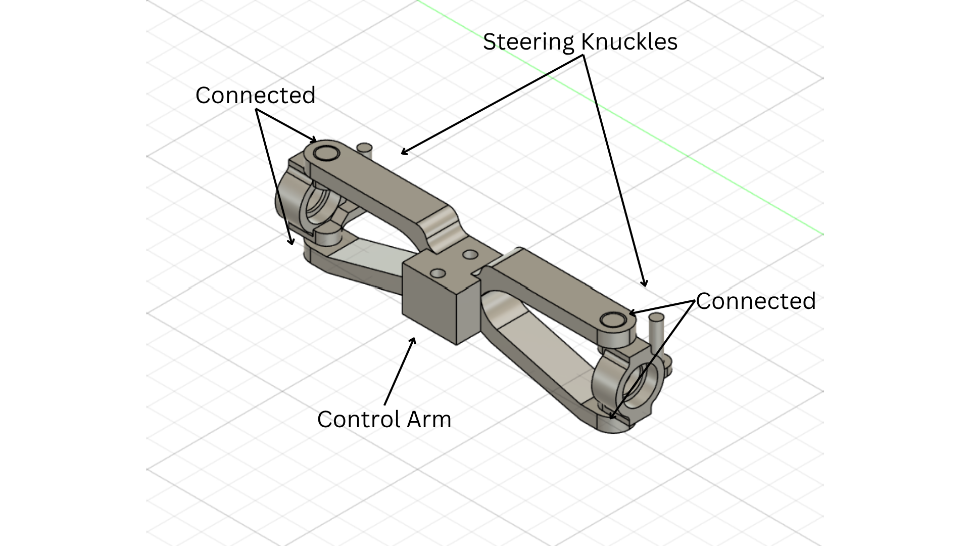
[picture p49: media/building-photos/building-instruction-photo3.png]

Connect both steering knuckles to the control arm.

---

### Step 4 — Mount steering to servo base
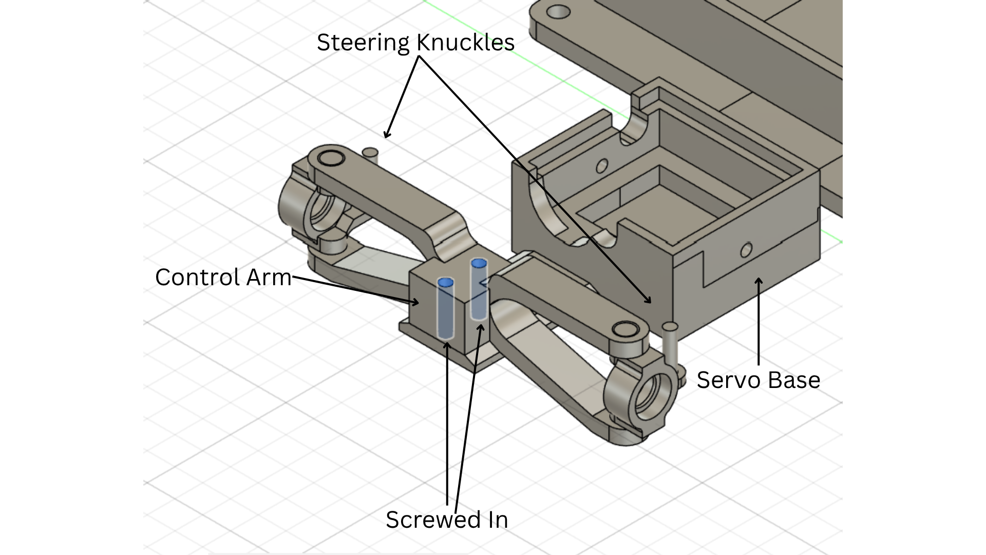
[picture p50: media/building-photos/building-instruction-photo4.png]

Screw the control-arm block onto the servo base.

---

### Step 5 — Prepare servo horn
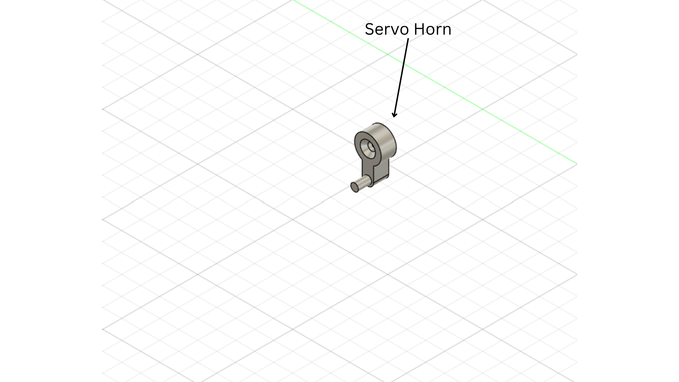
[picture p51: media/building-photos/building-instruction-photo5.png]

Place the horn on the servo output.

---

### Step 6 — Fix horn to servo
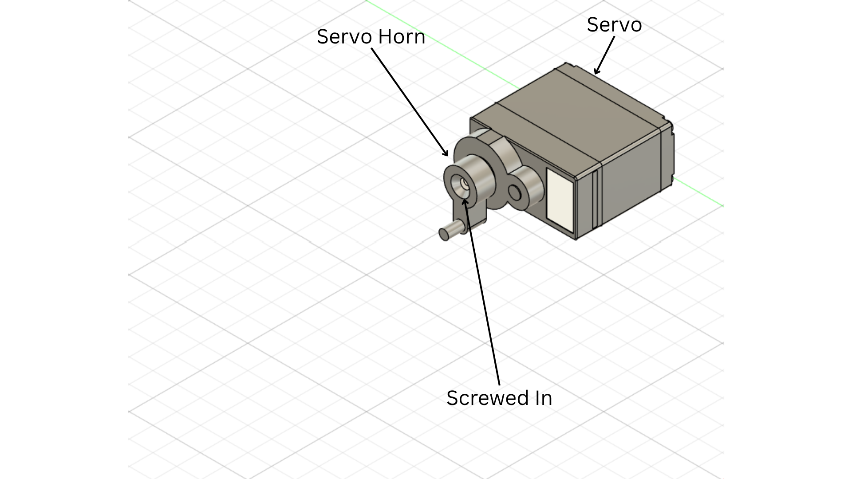
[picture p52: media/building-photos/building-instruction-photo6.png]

Tighten the horn screw.

---

### Step 7 — Add anti-sway arm
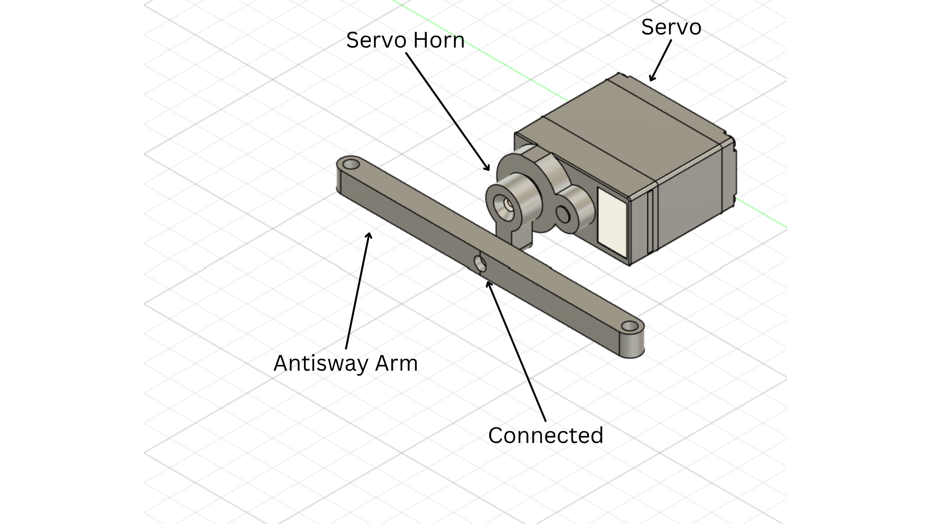
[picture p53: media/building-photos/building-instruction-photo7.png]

Connect the anti-sway arm to the horn.

---

### Step 8 — Complete steering linkage
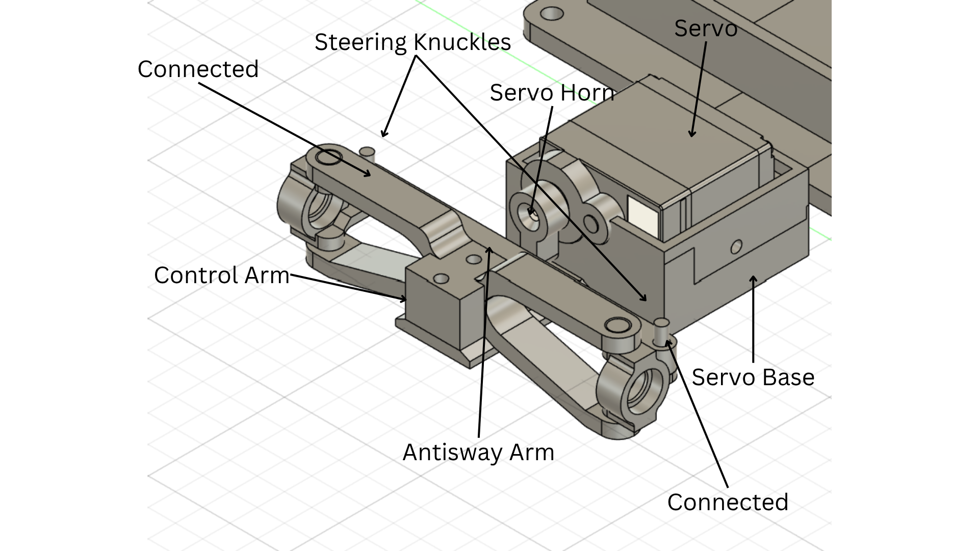
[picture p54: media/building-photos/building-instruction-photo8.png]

Join anti-sway arm to control arm; confirm free motion.

---

### Step 9 — Rear body mount: add bearings
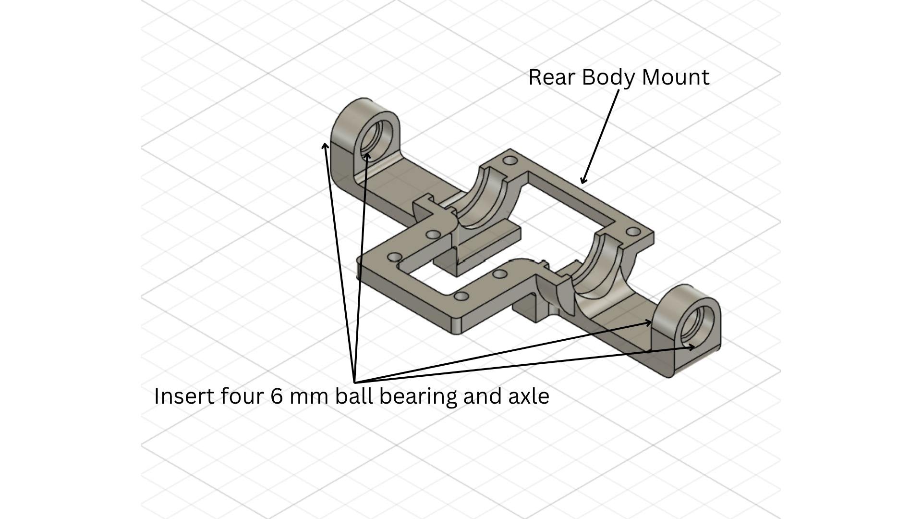
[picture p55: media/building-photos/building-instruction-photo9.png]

Insert four 6 mm bearings and axles.

---

### Step 10 — Rear axle & wheel prep
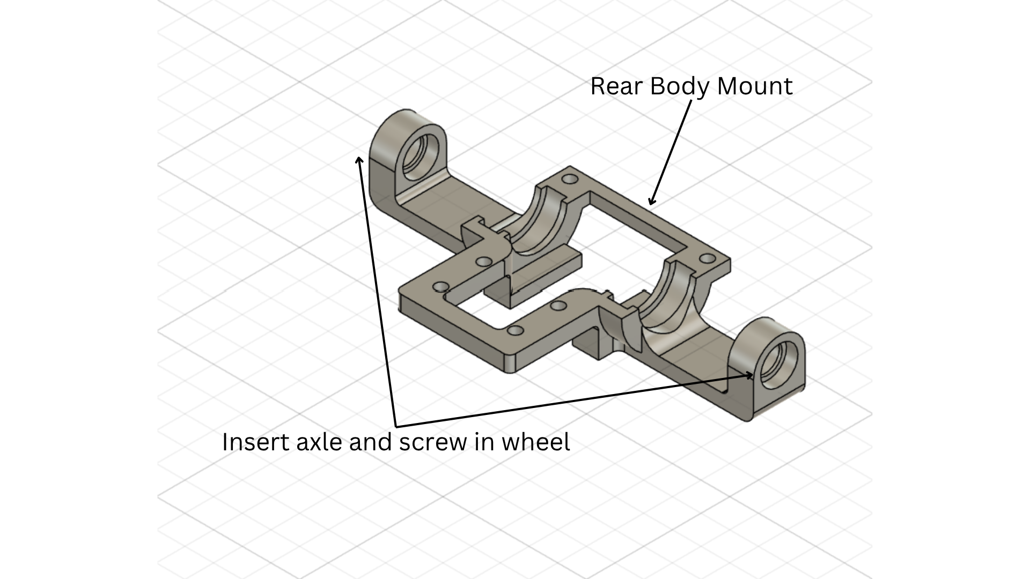
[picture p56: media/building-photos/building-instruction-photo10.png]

Insert axle and secure wheel.

---

### Step 11 — Install T-joint axle and gear
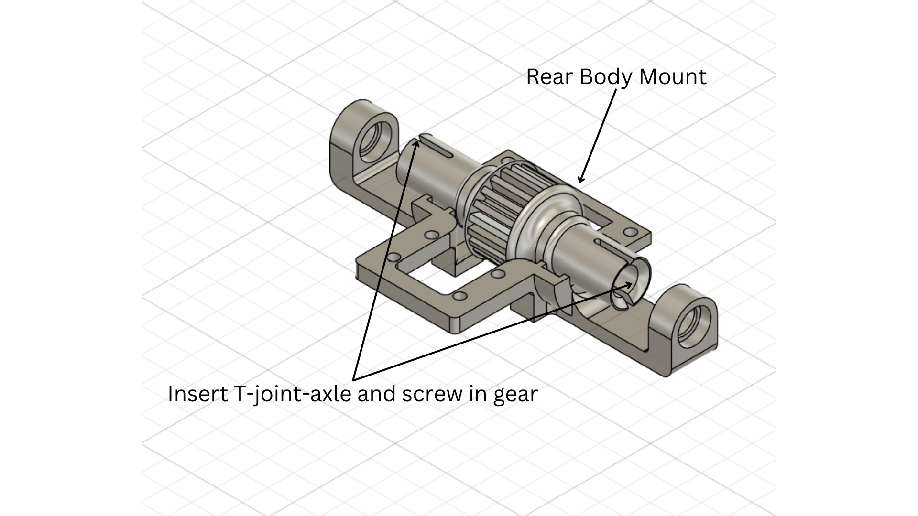
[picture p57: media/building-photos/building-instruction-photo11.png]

Slide in T-joint axle; screw on the main gear.

---

### Step 12 — Attach motor mount
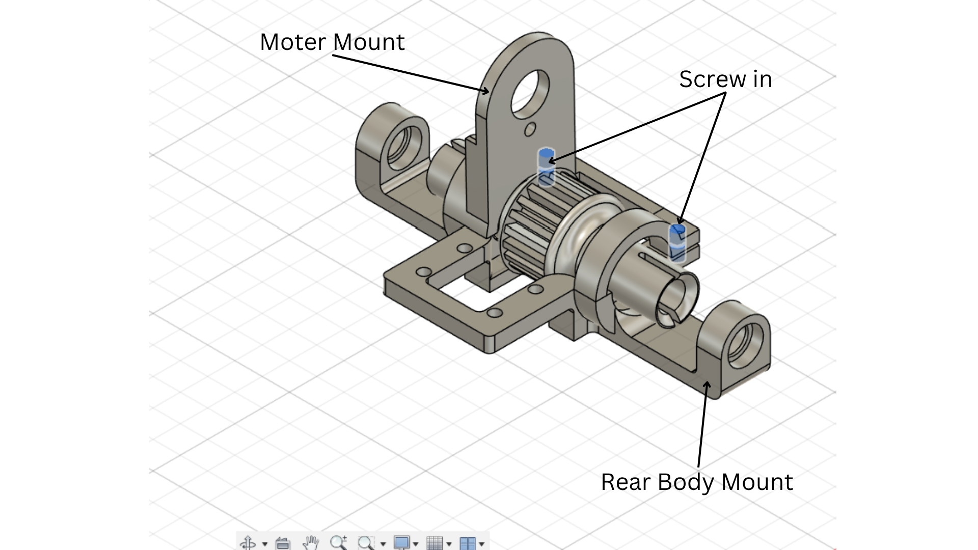
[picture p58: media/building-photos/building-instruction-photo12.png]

Bolt the motor mount to the rear assembly.

---

### Step 13 — Mount the motor
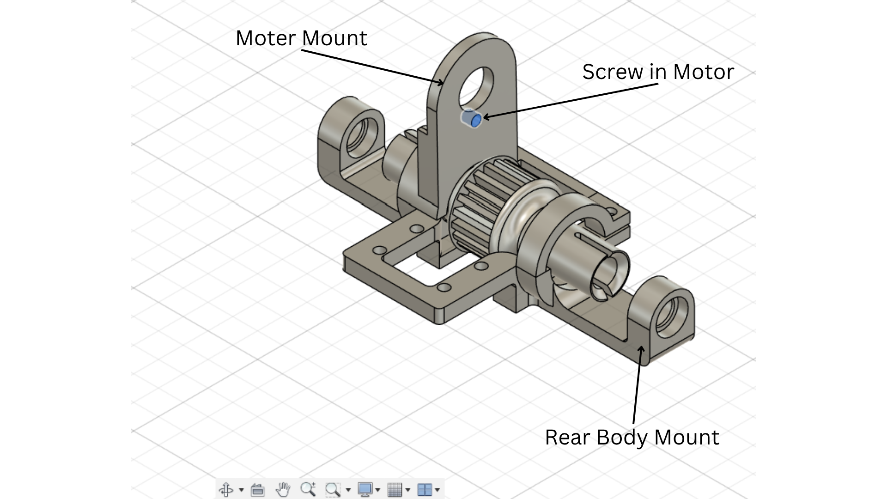
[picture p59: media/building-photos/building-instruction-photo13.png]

Screw the motor to the mount.

---

### Step 14 — Add small motor gear
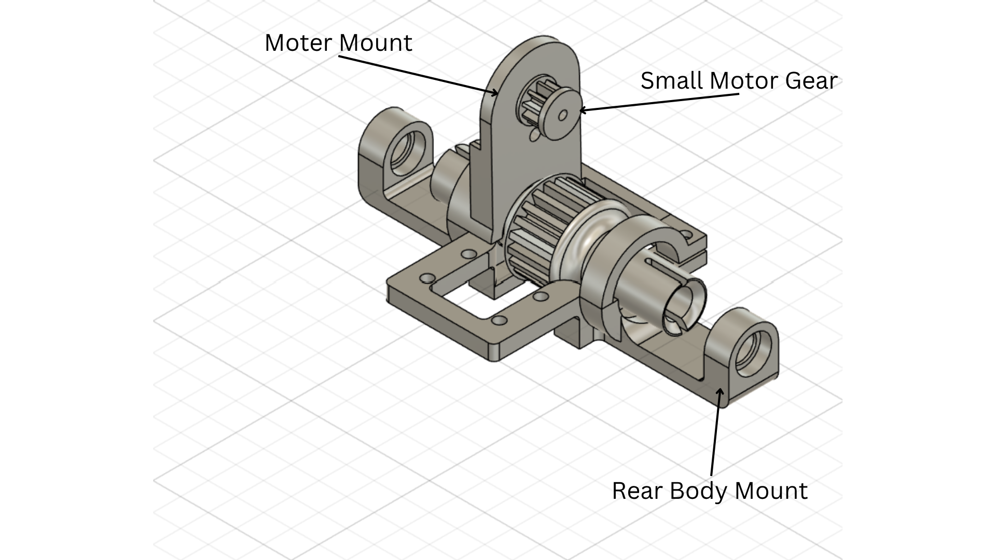
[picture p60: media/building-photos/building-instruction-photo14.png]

Secure the pinion on the motor shaft.

---

### Step 15 — Belt and rear assembly install
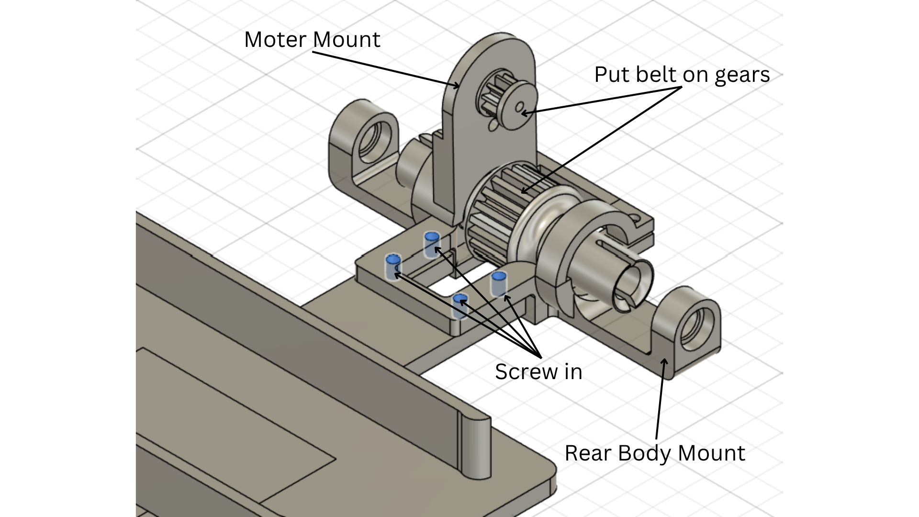
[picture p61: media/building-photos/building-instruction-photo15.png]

Loop belt over both gears; screw assembly to chassis.

---

### Step 16 — Chassis overview
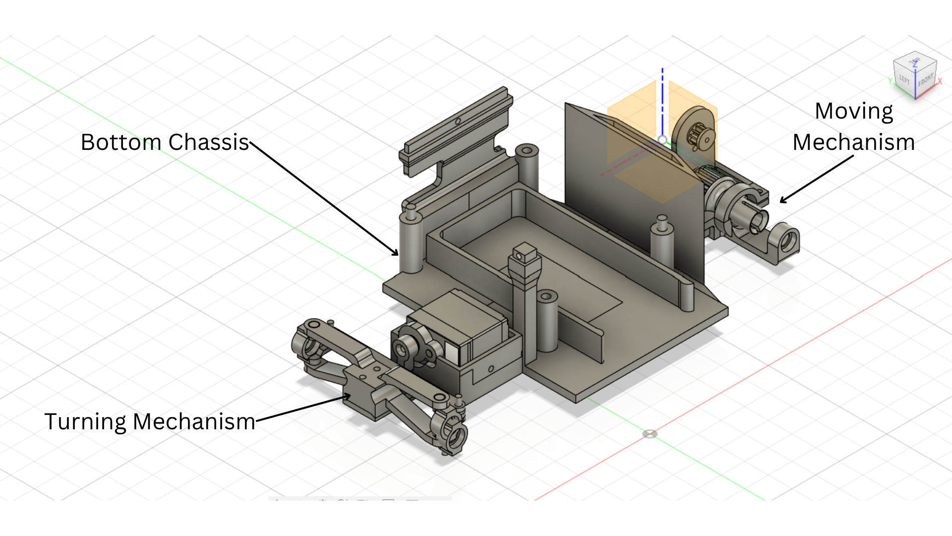
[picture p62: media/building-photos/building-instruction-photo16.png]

Identify bottom chassis, turning mechanism, and drive module.

---

### Step 17 — Mount RRC Lite controller
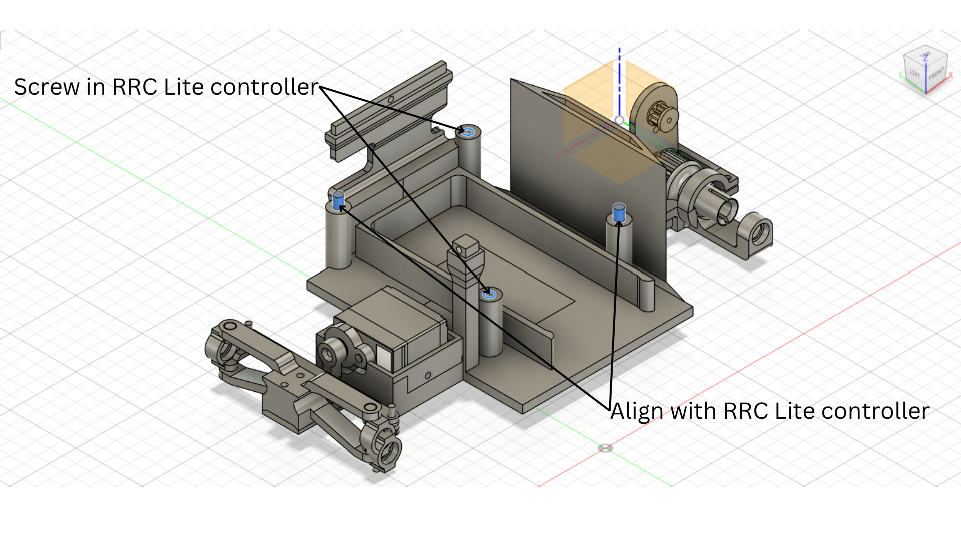
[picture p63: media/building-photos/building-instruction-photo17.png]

Align controller posts; screw in firmly.

---

### Step 18 — Add top chassis & Pi mount
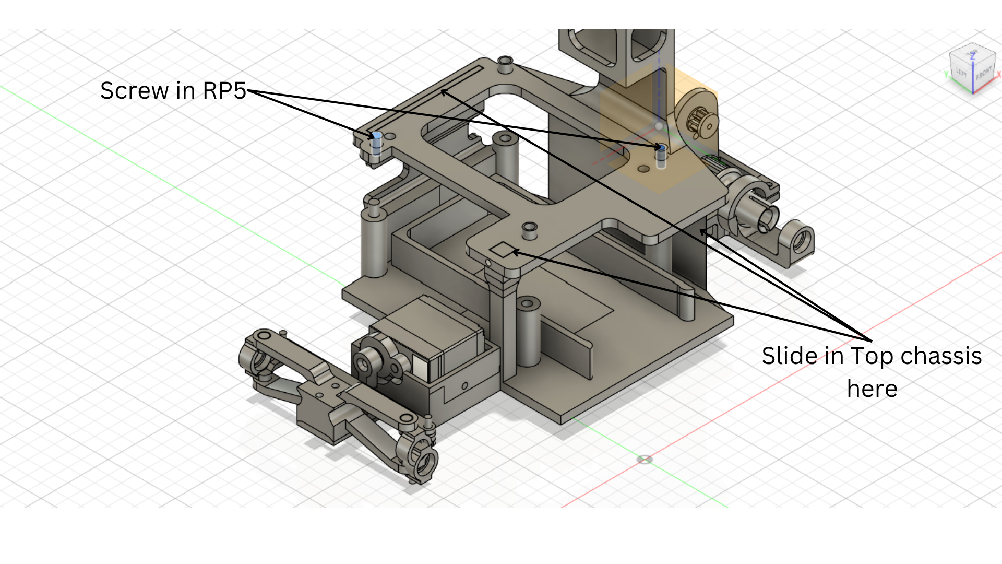
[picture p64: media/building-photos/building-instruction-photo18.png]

Slide in the top plate; screw down Raspberry Pi 5.

---

### Step 19 — Install ESC
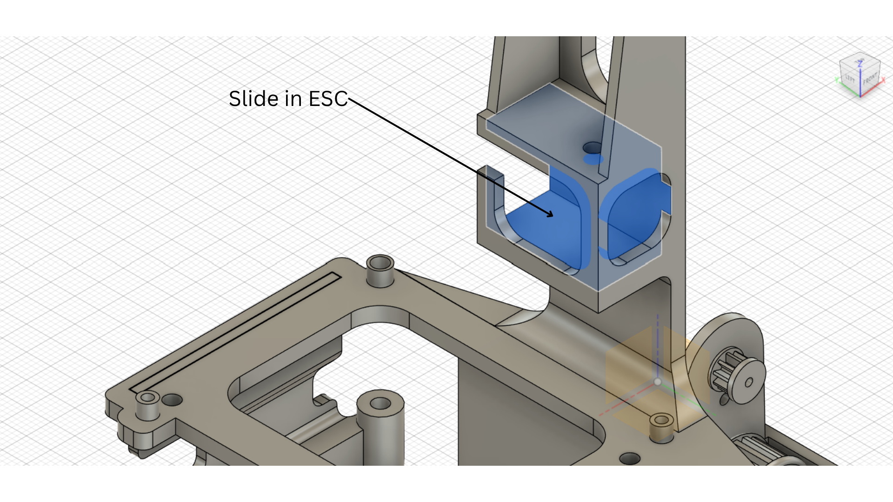
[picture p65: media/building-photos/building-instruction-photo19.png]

Slide the ESC into the tower slot.

---

### Step 20 — Mount camera plate
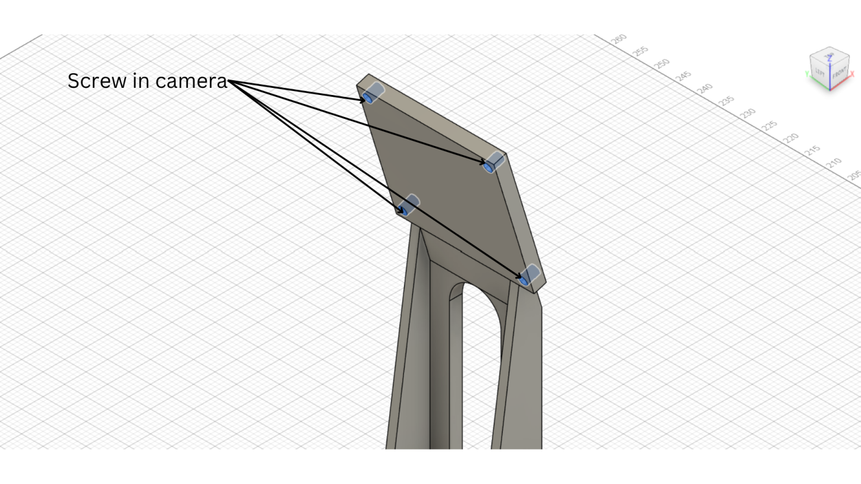
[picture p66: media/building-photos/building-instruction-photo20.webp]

Screw camera to the top plate (four points).

---

</br>

# Software Instructions

Since we use a CSI camera, we need to use picamera2. The problem with this is that we use ROS2 and picamera2 cannot be installed in a ROS2 docker container.

There are 3 possible solutions:

**Option1:** Use USB camera instead of CSI camera. A USB camera can be accessed without picamera2.

**Option2:** Split the project into two parts:
- Create a ROS2 node that runs on a Raspberry Pi host (instead of inside docker container). This node
publishes camera-related data
- Create the main ROS2 project in the docker container. It subscribes to the topic that publishes
camera data. It contains the main logic of the project.

**Option3:** Create the whole ROS2 project in a Raspberry pi host. It can access the camera via picamera2. It
also subscribes topics published by third-party ROS nodes in ROS2 container

*Note: Both options 2 and 3 require you to build a ROS2 environment from source in Raspberry Pi OS.*

We did not want to use a USB camera, instead we opted to build a ROS2 environment from source.

## Building the Environment

#### 1. Build a ROS2 environment from source in Raspberry Pi OS

</br>
   
#### 2. Switch from AP mode to STA mode so that Raspberry Pi has access to the internet
- Run command “nano hiwonder-toolbox/wifi_conf.py”, edit the file with your wifi and password.
Save the changes and reboot via command “sudo reboot”
- In the WIFI_STA_SSID, uncomment it if commented and type in your desired wifi SSID.
- In the WIFI_STA_PASSWORD, uncomment it if commented and type in your wifi password.

*Make sure to type in these correctly. If typed in incorrectly, you may need to reflash your SD card.*

</br>

<div align="center">

<table>
  <tr>
    <td style="border: 200px solid black; padding: 5px;">
      
    </td>
  </tr>
</table>

</div>

</br>

#### 3. Find the IP address of your computer (which is connected to the same wifi access point) by running command “ipconfig” in windows command prompt.
*To open command prompt, hit windows + r and type in cmd.*

</br>

<div align="center">

<table>
  <tr>
    <td style="border: 200px solid black; padding: 5px;">
      
    </td>
  </tr>
</table>

</div>

</br>

#### 4. Use Advanced IP Scanner or Angry IP Scanner to find the IP address of your Raspberry Pi.
*The IP range to scan should be the same as your computer’s IP address. For example,
my computer’s IP address is 172.16.0.223. The scan range is 172.16.0.1~172.16.0.254 (or 255)
After the scan is complete, Uncheck “View-&gt;Show Dead”. Check “View-&gt;Show Details Pane” so that you
can see the detailed pane on the right side as shown below. Navigate through the list of devices
found, looking for “ROS Image …” as shown below.*

</br>

<div align="center">

<table>
  <tr>
    <td style="border: 200px solid black; padding: 5px;">
      
    </td>
  </tr>
</table>

</div>

</br>

#### 5. Create a new connection in RealVNC Viewer using the IP address of your Raspberry Pi as shown below, and connect to it.

</br>

<div align="center">

<table>
  <tr>
    <td style="border: 200px solid black; padding: 5px;">
      
    </td>
  </tr>
</table>

</div>

</br>

#### 6. Go into LX Terminal and type/paste in the following code.

### Step 1: Install System Dependencies
```
sudo curl -sSL https://raw.githubusercontent.com/ros/rosdistro/master/ros.asc | sudo apt-key add -
sudo sh -c 'echo "deb [arch=$(dpkg --print-architecture)] http://packages.ros.org/ros2/ubuntu $(lsb_release -cs) main" > /etc/apt/sources.list.d/ros2-latest.list'
sudo apt update && sudo apt upgrade -y
sudo apt install -y \
  build-essential cmake git wget curl gnupg lsb-release \
  libpython3-dev python3-colcon-common-extensions \
  python3-flake8 python3-pip python3-pytest-cov python3-rosdep \
  python3-setuptools python3-vcstool python3-numpy \
  libasio-dev libtinyxml2-dev libcunit1-dev unzip libyaml-dev
sudo apt install -y libfastcdr-dev libfastrtps-dev
sudo apt install -y python3-dev python3-numpy
```

### Step2: Initialize Rosdep
```
sudo rosdep init || true
rosdep update
```
### Step3: Create ROS2 Workspace and Clone Minimal ROS2 Sources
```
mkdir -p ~/fe_ws/src
cd ~/fe_ws
wget https://raw.githubusercontent.com/ros2/ros2/humble/ros2.repos
vcs import src < ros2.repos
```

### Step 4: Install ROS 2 Source Dependencies
```
cd ~/fe_ws
rosdep install --from-paths src --ignore-src -y --rosdistro humble \
--skip-keys="fastcdr fastrtps rti-connext-dds-6.0.1 urdfdom_headers"
```
### Step 5: Install Missing Custom Message 'ros_robot_controller_msgs/msg/ButtonState'
```
- use the command "docker ps -a" to find the container ID of 'MentorPi' 
- run "docker cp adb8457c2eec:/home/ubuntu/ros2_ws/src/driver/ros_robot_controller_msgs ~/fe_ws/src/"  
  where adb8457c2eec should be replaced by the container ID of 'MentorPi' you got from the previous step
```

### Step 6: Build The Workspace
```
colcon build --symlink-install --packages-skip-regex '^rviz' 
```

### Step 7: Switch to Bash and Reboot
```
chsh -s /bin/bash 
sudo reboot
```

### Step 8: Source Your Environment
```
echo "source ~/fe_ws/install/setup.bash" >> ~/.bashrc
source ~/.bashrc
```

### Step 9: Test with the Commands Below. The First Command Should List All the ROS2 Topics. The Second Command Will Wait for you to Press Button 1 or 2
```
ros2 topic list
ros2 topic echo /ros_robot_controller/button
```

### Additional Step: Go Back to AP Mode With DHCP Issue Prevented
- update hiwonder-toolbox/wifi_conf.py to switch from STA mode to AP mode
```
sudo nano /etc/dnsmasq.d/wifi_ap.conf
- Paste the content below and save it
interface=wlan0
dhcp-range=192.168.149.10,192.168.149.100,12h
bind-interfaces

sudo systemctl restart dnsmasq
sudo reboot
```

Congratulations! You have built a ROS2 environment under a Raspberry Pi Host and created a ROS2
workspace “fe_ws”. You can now create ROS2 packages and nodes in this workspace.

Suppose you combine both Hardware and Software, hooray! You have built our entire car!

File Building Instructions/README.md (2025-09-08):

# Building Instructions
- This directory includes building instructions for our car.

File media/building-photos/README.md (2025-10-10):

building-photos
====

This directory contains our building instruction photos/gifs.

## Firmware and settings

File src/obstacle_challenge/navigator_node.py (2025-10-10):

#!/usr/bin/env python3
import rclpy
from rclpy.node import Node
from sensor_msgs.msg import Image
from std_msgs.msg import Float32, String, Bool
from cv_bridge import CvBridge
from obstacle_challenge import ros_robot_controller_sdk as rrc
from ros_robot_controller_msgs.msg import ButtonState
import cv2
import numpy as np
import time

class NavigatorNode(Node):
    def __init__(self):
        super().__init__('navigator_node')
        self.bridge = CvBridge()
        self.board = rrc.Board()

        # Configuration
        self.kp = 0.08
        self.kd = 0.003

        # Pillar 
        self.pillar_cx = None
        self.pillar_cy = None
        self.pillar_detection_thresh = 1800
        self.pillar_clear_thresh = 100 
        self.front_wall_threshold = 7000    # If frontm ROI has this much black, wall is close
        self.side_wall_threshold = 2500
        self.screen_center_x = 320

        #Control
        self.straight_pwm = 1500
        self.throttle_pwm = 1600
        self.throttle_prev = 1600
        self.angle_pwm = 1500
        self.max_left = 1850
        self.max_right = 1150
        self.current_angle = 0.0
        #Park / Stop
        self.stop_timer = 3.0

        self.left_roi = (0, 200, 180, 200)  # x, y, w, h
        self.right_roi = (460, 200, 180, 200)
        self.center_roi = (0, 180, 639, 260)  # x, y, w, h
        self.front_wall_roi = (260, 200, 160, 180)    # Upper center for front walls
        self.left_wall_roi = (100, 300, 60, 60)     # Left side walls
        self.right_wall_roi = (480, 300, 60, 60)   # Right side walls
        
        self.lower_red1 = np.array([0, 120, 50])
        self.upper_red1 = np.array([5, 255, 255])
        self.lower_red2 = np.array([175, 120, 50])
        self.upper_red2 = np.array([179, 255, 255])
        self.lower_green = np.array([50, 150, 80])
        self.upper_green = np.array([95, 255, 255])
        self.lower_magenta = np.array([150, 100, 80])
        self.upper_magenta = np.array([170, 255, 255])
        
        self.lower_orange = np.array([5, 100, 100])
        self.upper_orange = np.array([20, 255, 255])
    
        # State
        self.parking_side = None
        self.pillar_mode = None
        self.escape_start_time = 0
        self.last_pillar_time = 0
        self.prev_diff = 0
        self.prev_angle = self.straight_pwm
        self.left_area = 0
        self.right_area = 0
        self.left_red_area = 0
        self.center_red_area = 0
        self.right_green_area = 0
        self.center_green_area = 0
        self.lap_done_time = None
        self.frame_ready = False
        self.pillar_close = False
        self.wall_in_front = False
        self.right_wall_close = False   
        self.left_wall_close = False
        self.last_pillar = None
        self.mode = "button"

        """
        RGB COLOURS:
        GREEN: Green pillar detected
        RED: Red pillar detected
        MAGENTA: NOTHING DECTED PD steering
        STATES:
        1. button: wait for button press
        2. start: escape parking lot
        3. navigate: navigate 3 laps around track
        4. park: parallel parking
        5. stop: shutdown all nodes and stop moving 
        """
    
        # ROS 2
        self.create_subscription(Image, '/image_raw', self.camera_callback, 10)
        self.create_subscription(Bool, '/lap_status', self.lap_callback, 10)
        self.create_subscription(Float32, '/imu_angle', self.imu_callback, 10)
        self.create_subscription(ButtonState, '/ros_robot_controller/button', self.button_callback, 10)
        self.state_pub = self.create_publisher(String, '/state', 10)
        self.timer = self.create_timer(0.05, self.drive_callback)
        
        # Initialize board
        self.board.pwm_servo_set_position(0.1, [[4, 1500], [2, 1500]])
        time.sleep(2)
        self.board.set_rgb([[1, 255, 0, 255], [2, 255, 0, 255]])
    
    def button_callback(self, msg: ButtonState):
        if msg.id == 2 and msg.state == 1 and self.mode == "button":
            self.mode = "navigate"
        else:
            self.board.set_rgb([[1, 0, 255, 255], [2, 0, 255, 255]])
            
            
    def lap_callback(self, msg):
        if msg.data and self.mode != 'park':
            self.get_logger().info("Received IMU signal: 3 laps complete, switching to parking mode.")
            self.mode = 'park'
            self.lap_done_time = time.time()
        
    def imu_callback(self, msg):
        self.current_angle = msg.data
        if self.current_angle >= 800 and self.mode == "navigate":
            self.mode = "park"
    
    def camera_callback(self, msg):
        current_time = time.time()
        frame = self.bridge.imgmsg_to_cv2(msg, desired_encoding='rgb8')
    
        gray = cv2.cvtColor(frame, cv2.COLOR_RGB2GRAY)
        _, thresh = cv2.threshold(gray, 110, 255, cv2.THRESH_BINARY_INV)
    
        left_crop = thresh[self.left_roi[1]:self.left_roi[1]+self.left_roi[3], 
                            self.left_roi[0]:self.left_roi[0]+self.left_roi[2]]
        right_crop = thresh[self.right_roi[1]:self.right_roi[1]+self.right_roi[3], 
                            self.right_roi[0]:self.right_roi[0]+self.right_roi[2]]
        front_wall_crop = thresh[self.front_wall_roi[1]:self.front_wall_roi[1]+self.front_wall_roi[3], 
                           self.front_wall_roi[0]:self.front_wall_roi[0]+self.front_wall_roi[2]]
        left_wall_crop = thresh[self.left_wall_roi[1]:self.left_wall_roi[1]+self.left_wall_roi[3], 
                            self.left_wall_roi[0]:self.left_wall_roi[0]+self.left_wall_roi[2]]
        right_wall_crop = thresh[self.right_wall_roi[1]:self.right_wall_roi[1]+self.right_wall_roi[3], 
                            self.right_wall_roi[0]:self.right_wall_roi[0]+self.right_wall_roi[2]]
    
        
        center_color_crop = frame[self.center_roi[1]:self.center_roi[1]+self.center_roi[3], 
                            self.center_roi[0]:self.center_roi[0]+self.center_roi[2]]
        #Pd steering
        self.left_area = cv2.countNonZero(left_crop)
        self.right_area = cv2.countNonZero(right_crop)
        #pillar steering
        self.front_wall_area = cv2.countNonZero(front_wall_crop)
        self.left_wall_area = cv2.countNonZero(left_wall_crop)
        self.right_wall_area = cv2.countNonZero(right_wall_crop)

        hsv_center = cv2.cvtColor(center_color_crop, cv2.COLOR_RGB2HSV)

        
        center_magenta_mask = cv2.inRange(hsv_center, self.lower_magenta, self.upper_magenta)
        center_orange_mask = cv2.inRange(hsv_center, self.lower_orange, self.upper_orange)
                
        center_green_mask = cv2.inRange(hsv_center, self.lower_green, self.upper_green)
        center_red_mask = cv2.bitwise_or(cv2.inRange(hsv_center, self.lower_red1, self.upper_red1), 
                                cv2.inRange(hsv_center, self.lower_red2, self.upper_red2))
        
        center_red_mask = cv2.subtract(center_red_mask, center_magenta_mask)
        center_red_mask = cv2.subtract(center_red_mask, center_orange_mask)
        
        # Count pixels
        self.center_magenta_area = cv2.countNonZero(center_magenta_mask)
        self.center_green_area = cv2.countNonZero(center_green_mask)
        self.center_red_area = cv2.countNonZero(center_red_mask)

        if self.front_wall_area >= self.front_wall_threshold:
            self.wall_in_front = True
            #self.get_logger().info("Wall is close")
        else:
            self.wall_in_front = False
            #self.get_logger().info("Wall is no longer close")
        
        if self.left_wall_area >= self.side_wall_threshold:
            self.left_wall_close = True
            self.right_wall_close = False
            #self.get_logger().info("Wall is close")
        elif self.right_wall_area >= self.side_wall_threshold:
            self.right_wall_close = True
            self.left_wall_close = False
            #self.get_logger().info("Wall is close")    
        else:
            self.left_wall_close = False
            self.right_wall_close = False
            #self.get_logger().info("Wall is no longer close")
            
        # Pillar detection
        current_time = time.time()
        if self.pillar_mode is not None:
            current_pillar_area = self.center_red_area if self.pillar_mode == "red" else self.center_green_area
            if current_pillar_area >= self.front_wall_threshold:
                self.pillar_close = True
            else:
                self.pillar_close = False
            
        if self.center_red_area > self.pillar_detection_thresh and self.center_red_area > self.center_green_area:
            self.pillar_mode = "red" 
            self.last_pillar = "red"
            self.last_pillar_time = current_time
            self.prev_pillar_error = self.center_red_area
            self.get_logger().info("Entering RED pillar mode")
            self.board.set_rgb([[1, 255, 0, 0], [2, 255, 0, 0]])
            
        elif self.center_green_area > self.pillar_detection_thresh and self.center_green_area > self.center_red_area:
            self.pillar_mode = "green"  
            self.last_pillar = "green"
            self.last_pillar_time = current_time
            self.prev_pillar_error = self.center_green_area
            self.get_logger().info("Entering GREEN pillar mode")
            self.board.set_rgb([[1, 0, 255, 0], [2, 0, 255, 0]])

        else:
            #Exit condition
            current_pillar_area = self.center_red_area if self.pillar_mode == "red" else self.center_green_area
            # Use hysteresis to prevent flickering
            if (current_pillar_area < self.pillar_clear_thresh and 
                current_time - self.last_pillar_time > 0.1 and self.pillar_mode is not None):  # Wait 0.5s of low signal
                self.get_logger().info(f"Exiting {self.pillar_mode} pillar mode")
                self.pillar_mode = None
                self.board.set_rgb([[1, 255, 0, 255], [2, 255, 0, 255]])
            
        self.pillar_cx = None  # Reset centroid each frame
        self.pillar_cy = None
        if self.mode == "park" and self.center_magenta_area >= self.pillar_detection_thresh:
            # Find centroid
            M = cv2.moments(center_magenta_mask)
            if M["m00"] > 0:
                self.parking_cx = int(M["m10"] / M["m00"])
                self.parking_cy = int(M["m01"] / M["m00"])
                self.pillar_cy = self.pillar_cy + self.center_roi[1]

        if self.pillar_mode == "red":
            # Find centroid
            M = cv2.moments(center_red_mask)
            if M["m00"] > 0:
                self.pillar_cx = int(M["m10"] / M["m00"])
                self.pillar_cy = int(M["m01"] / M["m00"])
                self.pillar_cy = self.pillar_cy + self.center_roi[1]

        elif self.pillar_mode == "green":
            # Find centroid
            M = cv2.moments(center_green_mask)
            if M["m00"] > 0:
                self.pillar_cx = int(M["m10"] / M["m00"])
                self.pillar_cy = int(M["m01"] / M["m00"])
                self.pillar_cy = self.pillar_cy + self.center_roi[1]
                
        if self.mode == "start":
            if self.left_area > self.right_area:
                self.parking_side = "left"
                self.get_logger().info("Parking lot detected on LEFT")
            elif self.right_area > self.left_area:
                self.parking_side = "right" 
                self.get_logger().info("Parking lot detected on RIGHT")
            self.escape_phase = "front"
            
        # DEBUG
        if self.pillar_mode is not None:
            self.get_logger().info(f"CENTROID X: {self.pillar_cx}, CENTROID Y: {self.pillar_cy}")
        self.get_logger().info(f"Center ROI -> Red: {self.center_red_area}, Green: {self.center_green_area}")
        self.get_logger().info("-" * 40)
    
        # Debug rois on frame
        frame = cv2.cvtColor(frame, cv2.COLOR_RGB2BGR)
        cv2.rectangle(frame, (self.left_roi[0], self.left_roi[1]), 
                        (self.left_roi[0] + self.left_roi[2], self.left_roi[1] + self.left_roi[3]), (255, 0, 0), 2)
        cv2.rectangle(frame, (self.right_roi[0], self.right_roi[1]), 
                        (self.right_roi[0] + self.right_roi[2], self.right_roi[1] + self.right_roi[3]), (0, 255, 0), 2)
        cv2.rectangle(frame, (self.center_roi[0], self.center_roi[1]), 
                        (self.center_roi[0] + self.center_roi[2], self.center_roi[1] + self.center_roi[3]), (0, 0, 255), 2)
        
        # NEW: Draw centroid if detected
        if self.pillar_cx is not None and self.pillar_cy is not None:
            cv2.circle(frame, (self.pillar_cx, self.pillar_cy), 10, (0, 255, 255), -1)  # Yellow circle
            cv2.circle(frame, (self.parking_cx, self.parking_cy), 10, (255, 255, 255), -1)  # White circle
            cv2.putText(frame, f"CX: {self.pillar_cx}", (self.pillar_cx + 15, self.pillar_cy), cv2.FONT_HERSHEY_SIMPLEX, 0.5, (0, 255, 255), 2)
            
        cv2.rectangle(frame, (self.front_wall_roi[0], self.front_wall_roi[1]), 
                    (self.front_wall_roi[0] + self.front_wall_roi[2], self.front_wall_roi[1] + self.front_wall_roi[3]), 
                    (255, 255, 0), 2)  # Cyan for front wall ROI
        cv2.rectangle(frame, (self.left_wall_roi[0], self.left_wall_roi[1]), 
                    (self.left_wall_roi[0] + self.left_wall_roi[2], self.left_wall_roi[1] + self.left_wall_roi[3]), 
                    (255, 0, 255), 2)  # Magenta for left wall ROI
        cv2.rectangle(frame, (self.right_wall_roi[0], self.right_wall_roi[1]), 
                    (self.right_wall_roi[0] + self.right_wall_roi[2], self.right_wall_roi[1] + self.right_wall_roi[3]), 
                    (0, 255, 255), 2)  # Yellow for right wall ROI
        
        cv2.putText(frame, f"Centroid X: {self.pillar_cx}", (10, 90), cv2.FONT_HERSHEY_SIMPLEX, 0.6, (255, 255, 0), 2)
            
        # NEW: Add pillar mode and centroid info to display
        cv2.putText(frame, f"State: {self.mode}", (10, 30), cv2.FONT_HERSHEY_SIMPLEX, 0.6, (255, 255, 0), 2)
        cv2.putText(frame, f"Pillar: {self.pillar_mode}", (10, 60), cv2.FONT_HERSHEY_SIMPLEX, 0.6, (255, 255, 0), 2)

        cv2.imshow("Navigator Live Feed", frame)
        cv2.waitKey(1)

        self.frame_ready = True
    
    def drive_callback(self):
        if not self.frame_ready or self.mode == "button":
            return
        current_time = time.time()

        if self.mode == "start":
            if self.parking_side == "left":
                #1
                self.board.pwm_servo_set_position(0.1, [[2, 1570]])
                self.board.pwm_servo_set_position(0.1, [[4, self.max_right]])
                time.sleep(2.3)
                #2
                self.board.pwm_servo_set_position(0.1, [[2, 1420]])
                self.board.pwm_servo_set_position(0.1, [[4, self.max_left]])
                time.sleep(2.3)
                #3
                self.board.pwm_servo_set_position(0.1, [[2, 1570]])
                self.board.pwm_servo_set_position(0.1, [[4, self.max_right]])
                time.sleep(2.3)
                #4
                self.board.pwm_servo_set_position(0.1, [[2, 1420]])
                self.board.pwm_servo_set_position(0.1, [[4, self.max_left]])
                time.sleep(2.3)
                #5
                self.board.pwm_servo_set_position(0.1, [[2, 1420]])
                self.board.pwm_servo_set_position(0.1, [[4, self.max_left]])
  

                self.mode = "navigate"

            else:
                self.board.pwm_servo_set_position(0.1, [[2, 1570]])
                self.board.pwm_servo_set_position(0.1, [[4, self.max_left]])
                time.sleep(2.3)
                #2
                self.board.pwm_servo_set_position(0.1, [[2, 1420]])
                self.board.pwm_servo_set_position(0.1, [[4, self.max_right]])
                time.sleep(2.3)
                #3
                self.board.pwm_servo_set_position(0.1, [[2, 1570]])
                self.board.pwm_servo_set_position(0.1, [[4, self.max_left]])
                time.sleep(2.3)
                #4
                self.board.pwm_servo_set_position(0.1, [[2, 1420]])
                self.board.pwm_servo_set_position(0.1, [[4, self.max_right]])
                time.sleep(2.3)
                
                
                self.mode = "navigate"

        if self.pillar_mode and self.mode != "start" and self.mode != "button" and self.mode != "stop":
            current_time = time.time()
            
            if self.pillar_cx is not None:  
                if self.pillar_mode == "red":
                    error = self.pillar_cx - self.screen_center_x + 225
                    steering_adjustment = -error * 1.5  
                    if self.pillar_close:
                        steering_adjustment -= 30
                    self.angle_pwm = self.straight_pwm + steering_adjustment
                    if self.wall_in_front or self.right_wall_close:
                        self.angle_pwm = self.max_left
                        self.get_logger().info("emergency left turn")
                    self.get_logger().info(f"Red pillar - CX: {self.pillar_cx}, Error: {error}, PWM: {self.angle_pwm}")
                    
                elif self.pillar_mode == "green":
                    error = self.pillar_cx - self.screen_center_x - 225
                    steering_adjustment = -error * 1.5
                    if self.pillar_close:
                        steering_adjustment += 30 
                    self.angle_pwm = self.straight_pwm + steering_adjustment
                    if self.wall_in_front or self.left_wall_close:
                        self.angle_pwm = self.max_right
                        self.get_logger().info("emergency right turn")
                    self.get_logger().info(f"Green pillar - CX: {self.pillar_cx}, Error: {error}, PWM: {self.angle_pwm}")
                
                else:
                    if self.pillar_mode == "red":
                        self.angle_pwm = self.straight_pwm - 200  # Gentle right turn                   
                    else:
                        self.angle_pwm = self.straight_pwm + 200  # Gentle left turn
                    self.get_logger().info(f"{self.pillar_mode} pillar - Centroid lost, using default turn")
                    error = self.prev_pillar_error
                
            # Apply limits
            self.angle_pwm = max(min(self.angle_pwm, self.max_left), self.max_right)
            self.throttle = self.throttle_pwm
            self.throttle_prev = self.throttle
            #self.prev_pillar_error = error
        
        else:
            self.board.set_rgb([[1, 255, 0, 255], [2, 255, 0, 255]])
            area_diff = self.right_area - self.left_area
            self.angle_pwm = int(self.straight_pwm + area_diff * self.kp + (area_diff - self.prev_diff) * self.kd)
            self.angle_pwm = max(min(self.angle_pwm, self.max_left), self.max_right)
            self.throttle = self.throttle_pwm
            self.throttle_prev = self.throttle
            if self.last_pillar == "red" and (self.wall_in_front or self.right_wall_close):
                self.angle_pwm = self.max_left
                self.get_logger().info("emergency left turn")
            elif self.last_pillar == "green" and (self.wall_in_front or self.left_wall_close):
                self.angle_pwm = self.max_right
                self.get_logger().info("emergency right turn")
            self.prev_diff = area_diff
        

        # Park
        if self.mode == "park":
            if time.time() - self.lap_done_time >= self.stop_timer:
                self.get_logger().info("Preparing for parallel parking")
                self.speed(1500)
                self.steer_pwm(1500)
                msg_out = String()
                msg_out.data = "stop"
                self.state_pub.publish(msg_out) #stop for now
                rclpy.shutdown()
                return

        # Apply controls
        self.speed(self.throttle)
        self.steer_pwm(self.angle_pwm)

    def speed(self, throttle):
        if self.throttle_pwm != self.throttle_prev: #prevent overloading the board
            self.board.pwm_servo_set_position(0.1, [[2, throttle]])

    def steer_pwm(self, angle):
        self.board.pwm_servo_set_position(0.1, [[4, int(angle)]])

def main(args=None):
    rclpy.init(args=args)
    node = NavigatorNode()
    try:
        rclpy.spin(node)
    except KeyboardInterrupt:
        pass
    finally:
        # Cleanup
        node.board.pwm_servo_set_position(0.1, [[4, 1500], [2, 1500]])
        node.board.set_rgb([[1, 0, 0, 0], [2, 0, 0, 0]])
        cv2.destroyAllWindows()
        node.destroy_node()
        rclpy.shutdown()

if __name__ == '__main__':
    main()

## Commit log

2025-04-27 Rename Screenshot 2025-04-27 115331.png to Schematic
2025-07-14 Added PD steering
2025-07-18 Changed configuration values and added turn timer
2025-08-19 Completed camera_node
    Node continuously captures camera frames from Pi Camera, publishing them to topic /image_raw about 10 times a second.
2025-08-21 Completed imu_node.py
    Node used to send angular data to main navigator node.
2025-08-22 Update navigator_node.py
    Added PD steering and turn detection from open challenge adapted for ROS 2.
2025-08-22 Update camera_node
    Fix image error by converting BGRA to BGR before publishing
2025-08-26 Update camera_node
    refactor main() for proper shutdown process
2025-08-26 Update imu_node.py
    add internal lap counting and clean shutdown
2025-08-27 Update README.md
    Added lidar, updated images.
2025-08-27 Create Motor Mechanism Instructions
2025-08-30 Update camera_node
    publish rgb frame instead of bgr
2025-08-30 Update navigator_node.py
    add pillar PD steering, HSV color masks, and better control structure
2025-09-07 Create schematic
2025-09-07 Rename README (2).md to schematic/README.md
2025-09-07 Update camera_node.py
    changed ros2 stop message system
2025-09-07 Update imu_node.py
    fixed issue with IMU data starting at a randomized angle
    [imu_node.py]
2025-09-07 Update open_challenge.py
    Fixed problem with turn exits and implemented button starts
    [open_challenge.py]
2025-09-07 Update navigator_node.py
    added pillar centroid detection, refracted pillar steering, and added button starts
2025-09-07 Rename SCH_Schematic1_2025-09-07.pdf to schematic/Schematic Diagram.png
2025-09-07 Rename Schematic Diagram.png to Schematic Diagram.pdf
2025-09-07 Rename SCH_Schematic1_1-P1_2025-09-07.png to schematic/Schematic Diagram
2025-09-07 Rename Schematic Diagram to Schematic Diagram.png
2025-09-07 Rename Schematic Diagram.png to SchematicDiagram.png
2025-09-08 Update and rename Future Engineer Chassis_.step to 3D Model/Chassis_.step
    [Chassis_.step]
2025-09-08 Update and rename Link.md to 3D Chassis Model Link.md
2025-09-08 Rename Future Engineer Chassis STL.stl to Entire Car STL.stl
    [Entire Car STL.stl]
2025-09-08 Update open_challenge.py
    Fixed bug in button starting
    [open_challenge.py]
2025-09-22 Update navigator_node.py
    Major overhaul to centroid based steering system and added preliminary parking lot escape.
2025-09-26 Update navigator_node.py
    Improved pillar steering and parking lot escape
2025-10-02 Update navigator_node.py
    Changed ROIs based on new camera angle and fixed parking.
    [navigator_node.py]
2025-10-04 Update open_challenge.py
    Navigate using PD steering only.
2025-10-09 Rename Untitled design (7).gif to full-chassis.gif
2025-10-10 Rename Untitled design (8).gif to steering-system.gif
2025-10-10 Rename Steering system for ryan.stl to steering-system.stl
    [steering-system.stl]
2025-10-10 Rename Entire Car (1).stl to entire-car.stl
    [entire-car.stl]
2025-10-10 Rename Chassis Bottem.stl to chassis-bottom.stl
    [chassis-bottom.stl]
2025-10-10 Rename Turning System.stl to motor-mechanism.stl
    [motor-mechanism.stl]
2025-10-10 Rename Lidar Stand.stl to lidar-stand.stl
    [lidar-stand.stl]
2025-10-10 Rename Chassis Top.stl to chassis-top.stl
    [chassis-top.stl]
2025-10-10 Rename Turning System STL.stl to old-turning-system.stl
    [old-turning-system.stl]
